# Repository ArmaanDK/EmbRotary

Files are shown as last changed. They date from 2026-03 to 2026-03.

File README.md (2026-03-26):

# EmbRotary
Designing a motorized base that can turn embroidery hoops at variable rates.

## Design Criteria
- Hold three embroidery hoops upright
- Spin embroidery hoops at distinct rotational speeds
- Easy to build
- Use 3D printed hoops that max-out the printbed of a Creality Ender 3 V2

## Plan
A 3D printed base that houses three continuous servo motors, a Raspberry Pi Pico, and three rotary potentiometers for speed control.
The hoops will slide into crevices from the top of the box, interfacing with a bearing-mounted pinion gear and a driving pinion gear attached to a continuous servo.
A USB-C PD power supply (5VDC/3A) powers the device, supplying a 5VDC power rail for the three continuous servos and Raspberry Pi Pico.
Three potentiometers connect, in parallel, between the Pico's 3V3 output and GND, with their wipers connected to three ADC pins on the Pico.

## Mechanical Description
A shaftless, vertical oriented, gravity-preloaded, free-floating spur gear is supported by meshing with two pinion gears below it.
One pinion gear is motor-driven, applying a tangential force to spin the spur gear.
The second pinion gear is a bearing-supported idler pinion which is positioned contralaterally to the driven pinion so the spur gear rotates around its own center axis.
Currently exploring a tapered retaining double-flange design for the pinion gears to provide a lateral restoring force to oppose axial migration of the spur gear.

## Documentation
- [Hardware Selection](Hardware/HardwareSelection.md) - component choices and rationale
- [Bill of Materials](Hardware/BOM.md) - parts list with quantities
- [Wiring / Pin Assignments](Hardware/Wiring.md) - GPIO pin assignments and power connections
- [Software Setup](Software/SETUP.md) - flashing MicroPython and deploying the script

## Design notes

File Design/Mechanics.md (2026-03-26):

# Mechanics

## Gears
### Description
The spur gear is positioned vertically and gravity-preloaded, held down by its own weight without an axle, meshing into two pinion gears below it.
Two pinion gears are positioned contralaterally, opposite to each other across the spur gear's sagittal<sup>[1](#footnote1)</sup> plane, providing opposing tangential and radial reaction forces.
Both pinion gears providing opposing reaction forces prevents radial or tangential translation of the spur gear's center.
Tapered retaining flanges on the pinion gears provides lateral restoring forces to oppose axial translation.
The driven pinion gear applies a tangential force on the teeth of the spur gear as well as a radial force from being positioned laterally from the spur gear's sagittal<sup>[1](#footnote1)</sup> plane.
Simultaneously, the idler pinion's contralateral opposing tangential and radial reaction forces combine with the driven pinion's, forming a force couple.
The combined forces of the two pinions apply a pure moment on the central spur gear, causing pure rotation about its geometric center.

### Specifications
#### Spur Gear
 - Standard: Metric
 - Pressure Angle: 20 deg
 - Module: 6.00
 - Number of Teeth: 30
 - Backlash: 0.00 mm
 - Root Fillet Radius: 2.00 mm
 - Gear Thickness: 10.00 mm
 - Pitch Diameter: 180.0 mm

### Analysis
The gravity-preload must exceed the radial separating force for the gears to retain their mesh without the spur gear lifting off.

$F_{r} = F_{t} \cdot \tan{\phi}$

---
<a name="footnote1">1</a>: More technically referred to as the diametral plane

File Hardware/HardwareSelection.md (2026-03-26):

# Hardware Selection
A breakdown of the hardware selected, as well as the rationale for each selection.

## Motors
Feetech FT90R
- Servos rotate at a slower rate than DC motors
- Can be more easily controlled without needing a complex motor control board handling PWM and transient protection
- Quick and easy to source on Amazon.ca for cross-country parallel building
- Adequate performance without breaking the budget ($29.98CAD for 4)

## Speed Control
Generic 10kΩ Linear Taper Rotary Potentiometers (×3)
- Linear taper gives a proportional voltage output across the full rotation range, making speed feel intuitive to the user
- 10kΩ resistance keeps current draw from the 3V3 rail negligible (~0.33 mA per pot at full deflection)
- Three pots in parallel draw at most ~1 mA total from 3V3 — well within the Pico's 300 mA output limit
- Standard jellybean value, available at any electronics retailer

## Microcontroller
Raspberry Pi Pico
- Jellybean part (~$4USD from raspberrypi.com)
- Adequate GPIO and ADC inputs for project
- MicroPython has more human-readable code for understandability outside of the technological field
- Accepts 5VDC input without needing stepping-down from an external circuit

## Power Cleaning
### Capacitors
Transients from servos when PWM triggers movement can drop the power rail voltage

#### Bulk Input Capacitor
Softens the startup, spec'd for a worst-case scenario of all motors stalling and the Pico at max power consumption (very unrealistic).

Three servos with spec'd stalling currents of $700mA @ 4.8V$ and $800mA @ 6V$, linearly interpolating:

$700 + \frac{800 - 700}{6 - 4.8}(5 - 4.8) = 716.7mA$

$3 \times 716.7mA = 2150mA$

Worst-case scenario spec for Raspberry Pi Pico @ 5V is 95.5 mA,

$I_{T} = I_{Servos} + I_{Pico}$

$I_{T} = 2150mA + 95.5mA = 2245.5mA$

Assuming a $100 \mu s$ response from the power supply and a goal voltage change of less than 5%,

$C = \frac{2.25 A \times 0.0001 s}{5V \times 0.05} = 900 \mu F $

Indicating a minimum $1000 \mu F$ capacitor would be appropriate for the bulk input capacitor.

#### Servo Decoupling Capacitors
Handles transients per-motor going back to the power rail.

$C = \frac{0.7167 \times 0.0001 s}{5V \times 0.05} = 286.7 \mu F$

Since the bulk capacitor will also handle transients, we can rely on $100-220 \mu F$ capacitors instead.

#### Servo Noise Abatement
Expected noise from PWM servo control is in the 10s of MHz range. Adding $100nF$ ceramic capacitors in parallel to the decoupling capacitors will help mitigate high-frequency switching noise from making its way to the power rail.

## Power Supply
[USB-C PD 65W Wall Adapter](https://www.amazon.ca/dp/B0DL5JJS5T), 5VDC/3A output connected directly to the device
- Intended for use as an art installation, so the power source needs to be flexible regardless of venue
- USB-C PD is compatible with a wide range of wall adapters and battery banks, allowing the piece to run from standard wall outlets or a portable battery depending on the display location
- A proprietary barrel jack wall adapter would tie the installation to a specific plug and power source
- USB-C PD negotiates 5V as its baseline profile, reliably delivering the required 5V/3A (15W — well within the 65W capacity of the selected adapter)

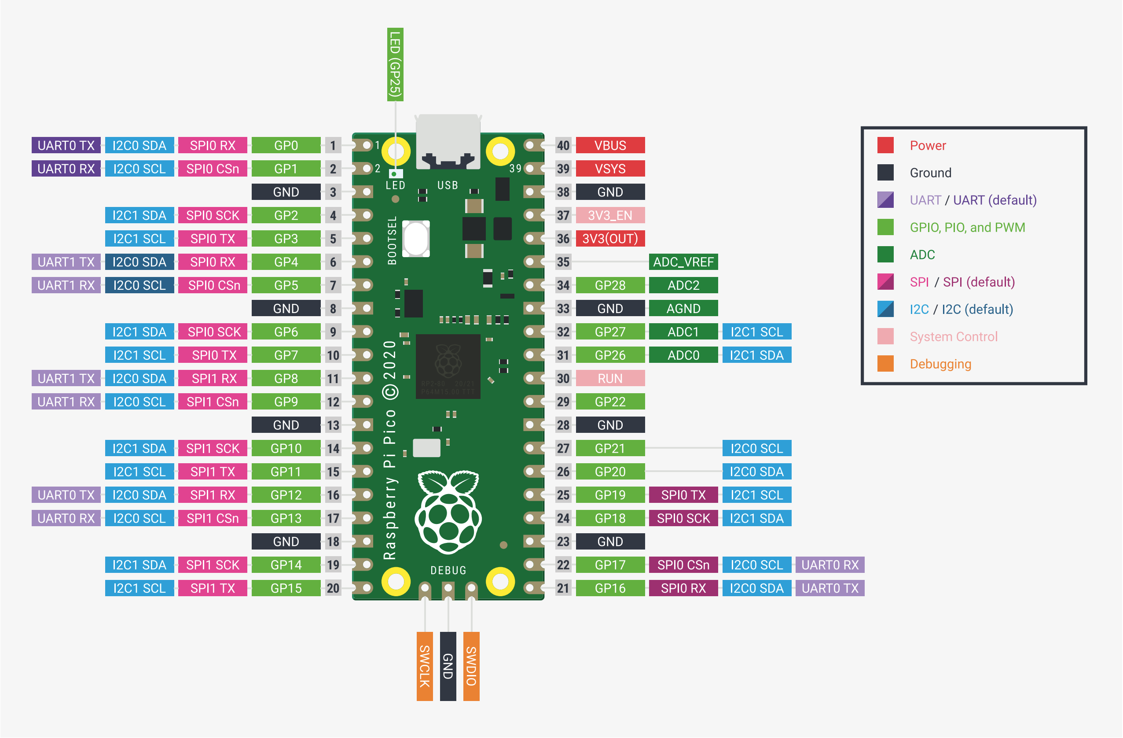
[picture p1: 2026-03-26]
Hardware/PI-PICO_PINOUT.png

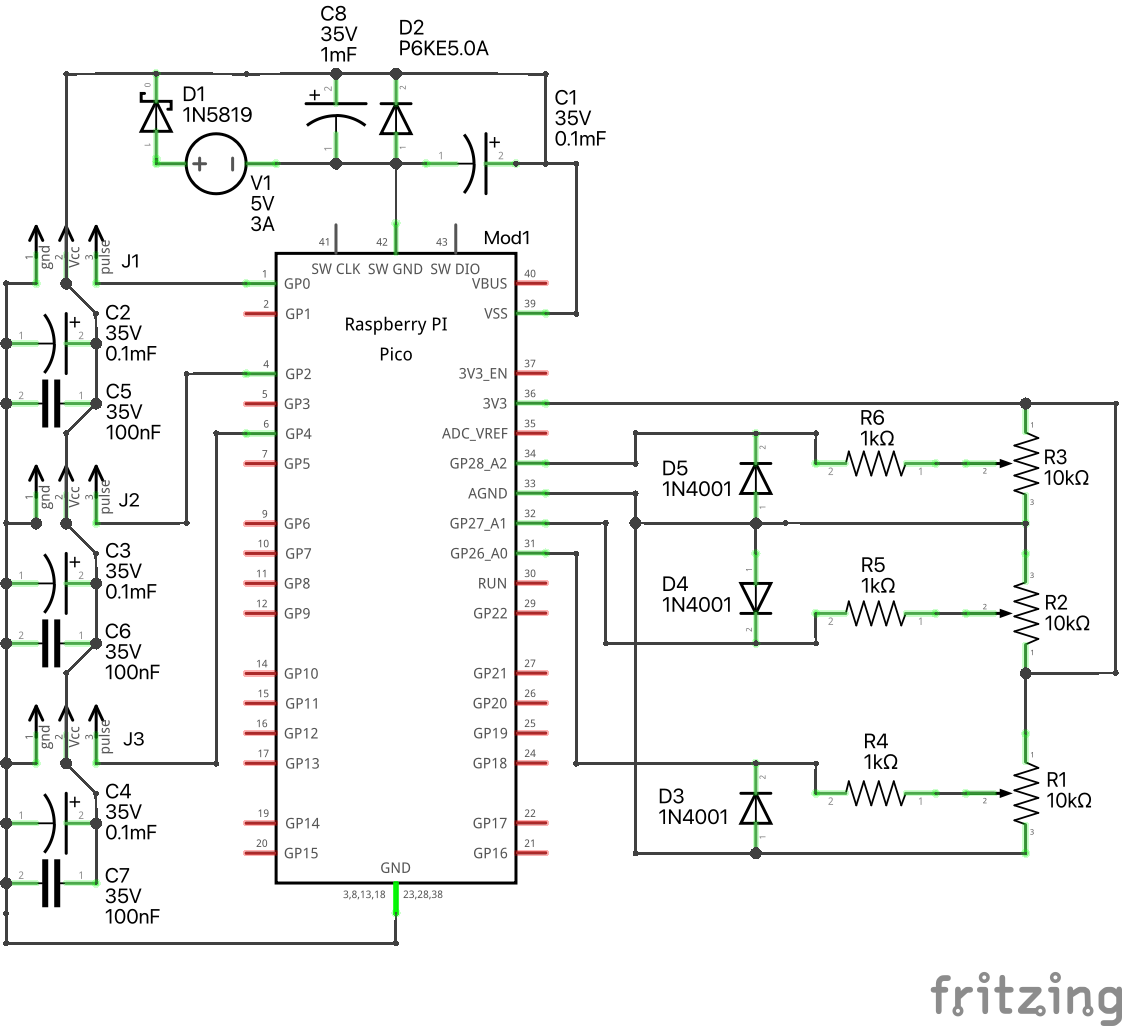
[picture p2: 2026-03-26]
Hardware/EmbRotary_Circuit_schem.png

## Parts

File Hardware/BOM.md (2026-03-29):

# Bill of Materials

Complete parts list for one EmbRotary unit.

---

## Power Path 

| | Path A — USB-C | Path B — DC Barrel Jack |
|---|---|---|
| **Soldering required?** | No | Yes |
| **Best for** | Prototyping / artist build | Permanent enclosure build |

Items marked **[A]** or **[B]** below apply only to that path. Unmarked items are required for both.

---

## Electronics

| Qty | Part | Value / Notes | Source |
|-----|---|---|---|
| 3 | Feetech FT90R Continuous Rotation Servo | Sold in 4-packs; 1 spare | [Amazon.ca][servo] |
| 1 | Raspberry Pi Pico | Pre-soldered headers recommended | [Amazon.ca][pico] |
| 3 | Rotary Potentiometer | 10kΩ linear taper, 15mm shaft (WH148) | [Amazon.ca][pots] |
| 3 | Potentiometer Knob | 6mm knurled shaft, 15×17mm — fits WH148 | [Amazon.ca][knobs] |
| 1 | Electrolytic Capacitor, 1000µF 25V | Bulk input decoupling | [Amazon.ca][ecaps] |
| 3 | Electrolytic Capacitor, 220µF 25V | Per-servo decoupling | [Amazon.ca][ecaps] |
| 3 | Ceramic Capacitor, 100nF | Per-servo high-frequency noise filter | [Amazon.ca][ccaps] |
| 1 | Schottky Diode | D1 — reverse polarity protection; 1N5819 | [Amazon.ca][diodes] |
| 4 | Rectifier Diode | D2–D5; 1N4001 or equivalent | [Amazon.ca][diodes] |
| 1 | Zener Diode | 3.3V BZX55C3V3 — ADC input clamping | [Amazon.ca][zener] |
| 1 | TVS Diode | P6KE6.8A, 600W — transient suppression | [Amazon.ca][tvs] |
| 3 | Resistor, 1kΩ | R4, R5, R6 — current limiting on ADC lines | [Amazon.ca][resistors] |

> Capacitors, diodes, and resistors are sold in assortment kits containing far more than one unit requires. Surplus can be shared between builds.

---

## Power

| Qty | Part | Value / Notes | Source |
|-----|---|---|---|
| 1 | USB-C Power Supply **[A]** | 5V/3A — plug-in, no soldering | [Amazon.ca][usbc-supply] |
| 1 | DC Wall Adapter **[B]** | 5V/3A, 5.5×2.1mm barrel jack output | [Amazon.ca][dc-supply] |
| 1 | Panel-Mount USB-C Socket **[B]** | 6-pin flush mount, PD 65W — soldered to hookup wire, nut-mounted to enclosure | [Amazon.ca][usbc-panel] |
| 1 | Hookup Wire Kit | 22 AWG, 7 colours, 26ft/spool | [Amazon.ca][wire] |
| 1 | Breadboard + Jumper Wire Kit **[A]** | 830+400pt boards, 200+ jumper wires | [Amazon.ca][breadboard] |

---

## Mechanical

| Qty | Part | Notes | Source |
|-----|---|---|---|
| 1 | 3D Printed Parts | Base, pinion gears, hoops — print files in `/Design` | See `/Design` |
| 6 | 625ZZ Ball Bearing | 5×16×5mm — drive and idler pinion per hoop (2× per hoop) | [Amazon.ca][bearings] |
| 1 | M2/M3/M4/M5 Screw Assortment | Alloy steel, black oxide — all printed assembly hardware | [Amazon.ca][screws] |
| 1 | Wood PLA Filament Bundle | 1.75mm, 30%+ real wood fibre, 4×200g — current print material | [Amazon.ca][filament] |

---

[servo]: https://www.amazon.ca/dp/B07JDR2HH5
[pico]: https://www.amazon.ca/Freenove-Raspberry-Compatible-Pre-Soldered-Development/dp/B09X33TBY3/
[pots]: https://www.amazon.ca/dp/B09XDR799P
[knobs]: https://www.amazon.ca/dp/B0C14MGL4B
[ecaps]: https://www.amazon.ca/dp/B0C1VBXCQM
[ccaps]: https://www.amazon.ca/dp/B08DNF191P
[diodes]: https://www.amazon.ca/dp/B08F2LHDZ7
[zener]: https://www.amazon.ca/dp/B07WDR4DBN
[tvs]: https://www.amazon.ca/dp/B0FRMZ2G2X
[resistors]: https://www.amazon.ca/ELEGOO-Resistor-Assortment-Compliant-Respberry/dp/B072BL2VX1/
[screws]: https://www.amazon.ca/dp/B0D6347484
[bearings]: https://www.amazon.ca/dp/B0CJFSBRTJ
[usbc-supply]: https://www.amazon.ca/Miuzei-Raspberry-Pi-Power-Supply/dp/B09WYRFWMW/
[dc-supply]: https://www.amazon.ca/BTF-LIGHTING-Certified-Transformer-Converter-SK6812RGBW/dp/B0G8JQ1FJ7/
[usbc-panel]: https://www.amazon.ca/dp/B0DL5JJS5T
[breadboard]: https://www.amazon.ca/Breadboards-Include-Solderless-Jumper-Tweezer/dp/B0BMFXPSVG/
[wire]: https://www.amazon.ca/dp/B083DN5R61
[filament]: https://www.amazon.ca/dp/B0C85SS6FT

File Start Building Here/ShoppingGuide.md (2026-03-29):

# EmbRotary - Quick Shopping Guide

---

## Step 1 — One Question First

**Do you have access to a soldering iron?**

- **No -> you're on Path A.** Skip the items marked [B] below.
- **Yes -> you're on Path B.** Skip the items marked [A] below.

---

## Step 2 — Order Everything on This List

### Core Electronics

| What | Price | Link |
|---|---|---|
| Feetech FT90R Servo (4-pack, 3 used) | CA$29.98 | [Amazon.ca][servo] |
| Raspberry Pi Pico (pre-soldered headers) | CA$17.95 | [Amazon.ca][pico] |
| 10kΩ Potentiometer WH148 (30-pack, 3 used) | CA$13.61 | [Amazon.ca][pots] |
| Potentiometer Knob 6mm (60-pack, 3 used) | CA$7.69 | [Amazon.ca][knobs] |

### Circuit Components *(kits — one purchase covers everything)*

| What | Price | Link |
|---|---|---|
| Electrolytic Capacitor Kit | CA$18.99 | [Amazon.ca][ecaps] |
| Ceramic Capacitor Kit | CA$24.99 | [Amazon.ca][ccaps] |
| Rectifier + Schottky Diode Kit | CA$11.25 | [Amazon.ca][diodes] |
| Zener Diode 3.3V (20-pack) | CA$8.00 | [Amazon.ca][zener] |
| TVS Diode P6KE6.8A (20-pack) | CA$9.00 | [Amazon.ca][tvs] |
| Resistor Kit (525-pack) | CA$13.99 | [Amazon.ca][resistors] |

### Mechanical

| What | Price | Link |
|---|---|---|
| 625ZZ Bearings 5×16×5mm (15-pack, 6 used) | CA$11.19 | [Amazon.ca][bearings] |
| M2–M5 Screw Assortment (860-piece) | CA$14.99 | [Amazon.ca][screws] |
| Wood PLA Filament Bundle 1.75mm, 4×200g | CA$39.99 | [Amazon.ca][filament] |

### Power + Wiring

| What | Price | Link |
|---|---|---|
| Miuzei USB-C Power Supply 5V/3A **[A]** | CA$17.99 | [Amazon.ca][usbc-supply] |
| Breadboard + Jumper Wire Kit **[A]** | CA$19.99 | [Amazon.ca][breadboard] |
| DC Wall Adapter 5V/3A barrel jack **[B]** | CA$17.09 | [Amazon.ca][dc-supply] |
| Panel-Mount USB-C Socket (5-pack) **[B]** | CA$19.11 | [Amazon.ca][usbc-panel] |
| 22 AWG Hookup Wire Kit | CA$21.98 | [Amazon.ca][wire] |

---

## Step 3 — Print the Parts

Print files are in the `/Design` folder of the repository. Use the Wood PLA filament ordered above.

---

[servo]: https://www.amazon.ca/dp/B07JDR2HH5
[pico]: https://www.amazon.ca/Freenove-Raspberry-Compatible-Pre-Soldered-Development/dp/B09X33TBY3/
[pots]: https://www.amazon.ca/dp/B09XDR799P
[knobs]: https://www.amazon.ca/dp/B0C14MGL4B
[ecaps]: https://www.amazon.ca/dp/B0C1VBXCQM
[ccaps]: https://www.amazon.ca/dp/B08DNF191P
[diodes]: https://www.amazon.ca/dp/B08F2LHDZ7
[zener]: https://www.amazon.ca/dp/B07WDR4DBN
[tvs]: https://www.amazon.ca/dp/B0FRMZ2G2X
[resistors]: https://www.amazon.ca/ELEGOO-Resistor-Assortment-Compliant-Respberry/dp/B072BL2VX1/
[bearings]: https://www.amazon.ca/dp/B0CJFSBRTJ
[screws]: https://www.amazon.ca/dp/B0D6347484
[filament]: https://www.amazon.ca/dp/B0C85SS6FT
[usbc-supply]: https://www.amazon.ca/Miuzei-Raspberry-Pi-Power-Supply/dp/B09WYRFWMW/
[breadboard]: https://www.amazon.ca/Breadboards-Include-Solderless-Jumper-Tweezer/dp/B0BMFXPSVG/
[dc-supply]: https://www.amazon.ca/BTF-LIGHTING-Certified-Transformer-Converter-SK6812RGBW/dp/B0G8JQ1FJ7/
[usbc-panel]: https://www.amazon.ca/dp/B0DL5JJS5T
[wire]: https://www.amazon.ca/dp/B083DN5R61

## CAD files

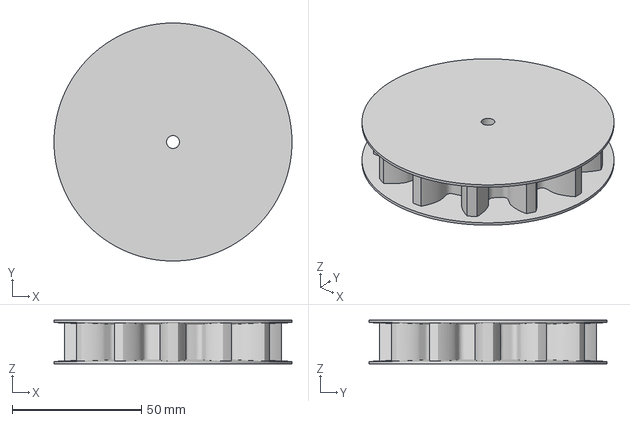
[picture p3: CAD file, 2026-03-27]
Design/Reference Models/Pinion (12 teeth).3mf
92.0 x 92.0 x 17.0 mm

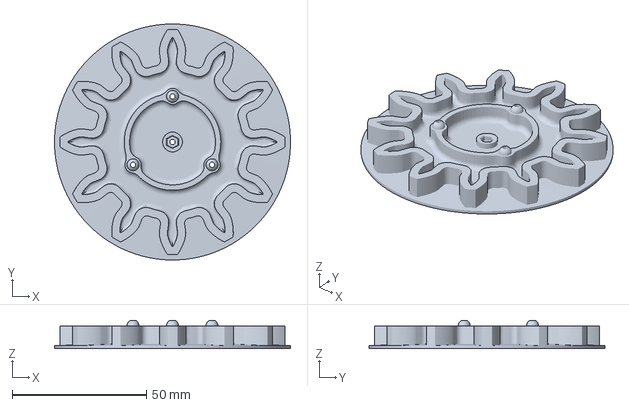
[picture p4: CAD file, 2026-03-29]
Start Building Here/PrintFiles/Half Pinion Gears/Pinion-Idler-S2.3mf
88.0 x 88.0 x 10.5 mm

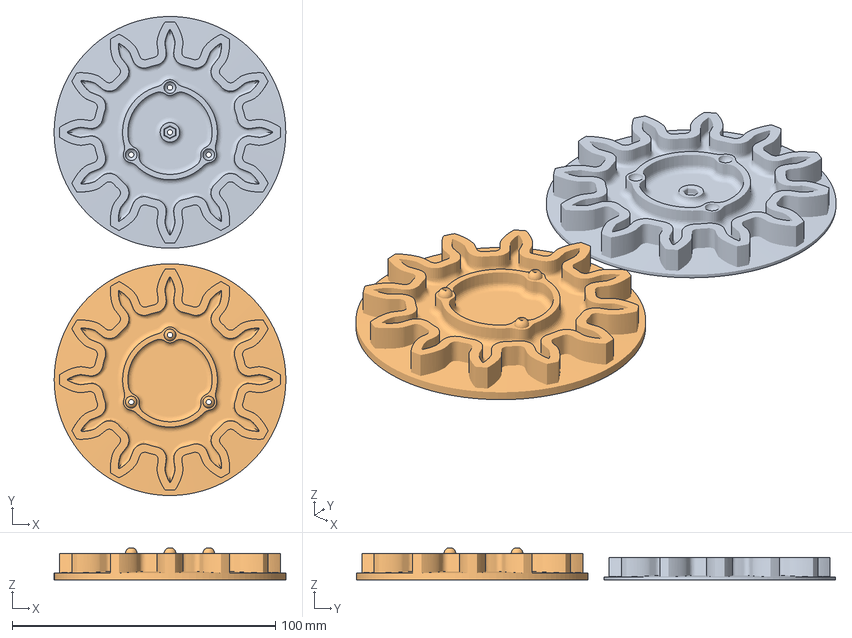
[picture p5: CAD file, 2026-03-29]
Start Building Here/PrintFiles/Pinion-Driver.3mf
88.0 x 182.0 x 12.0 mm
Pinion-Idler-S1
Pinion-Driver

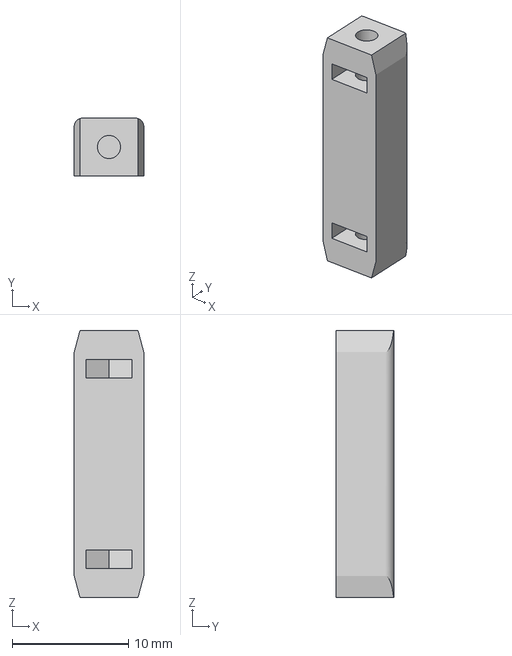
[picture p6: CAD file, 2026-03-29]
Start Building Here/PrintFiles/23mm-Connector.3mf
6.00 x 5.00 x 23.0 mm

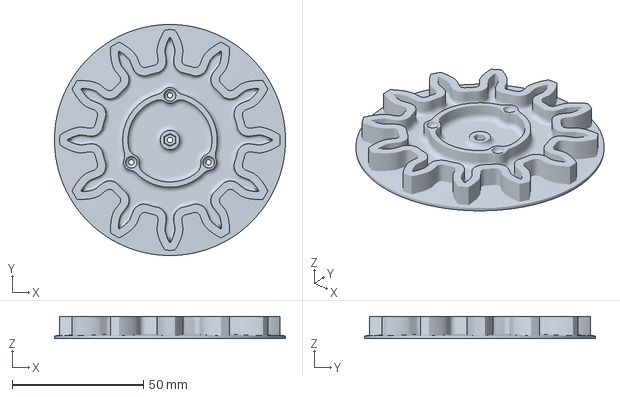
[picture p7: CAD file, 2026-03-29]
Start Building Here/PrintFiles/Half Pinion Gears/Pinion-Idler-S1.3mf
88.0 x 88.0 x 8.50 mm

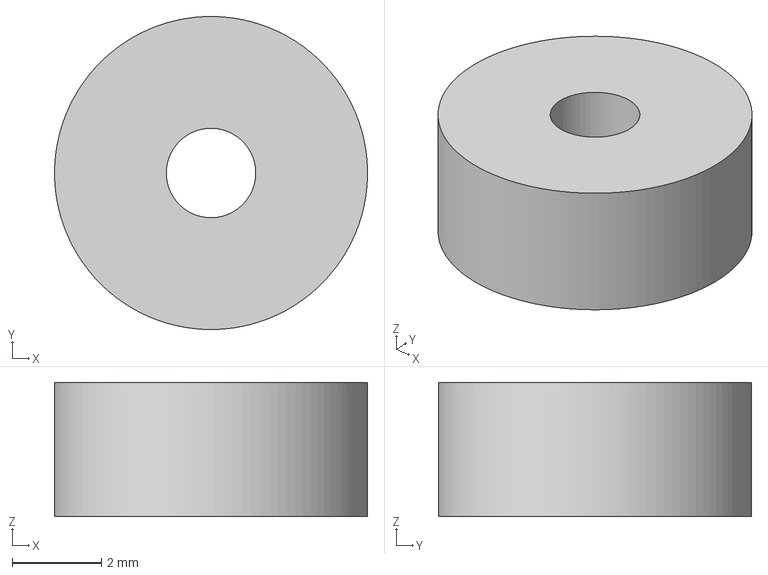
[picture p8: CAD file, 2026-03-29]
Start Building Here/PrintFiles/AxleSpacer.3mf
7.00 x 7.00 x 3.00 mm

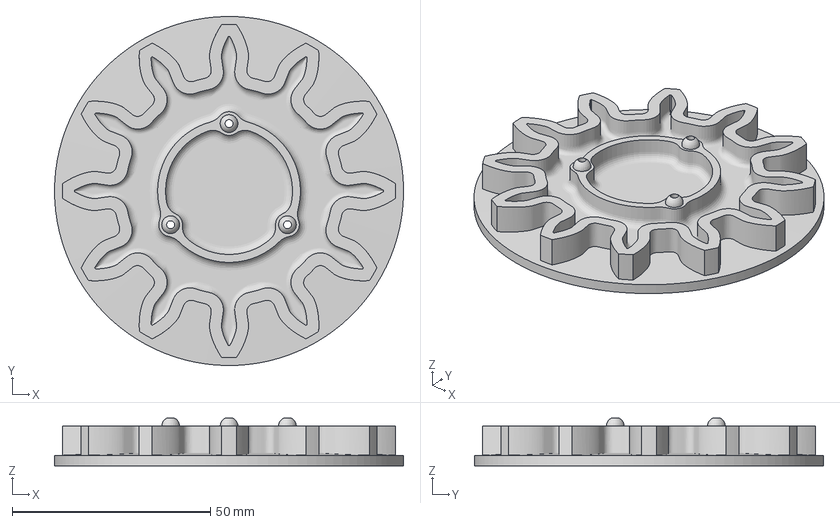
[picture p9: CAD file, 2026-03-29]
Start Building Here/PrintFiles/Half Pinion Gears/Pinion-Driver.3mf
88.0 x 88.0 x 12.0 mm

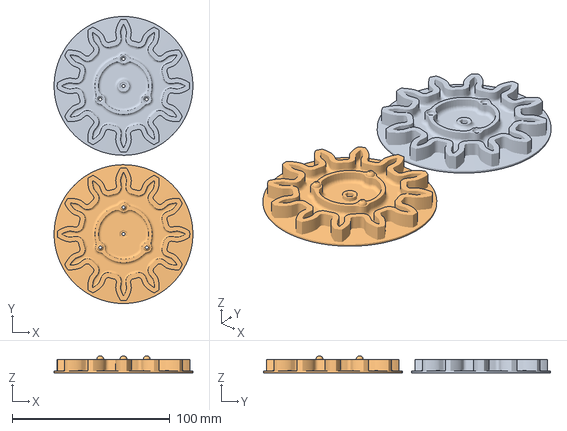
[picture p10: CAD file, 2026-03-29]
Start Building Here/PrintFiles/Pinion-Idler.3mf
88.0 x 182.0 x 10.5 mm
Pinion-Idler-S1
Pinion-Idler-S2

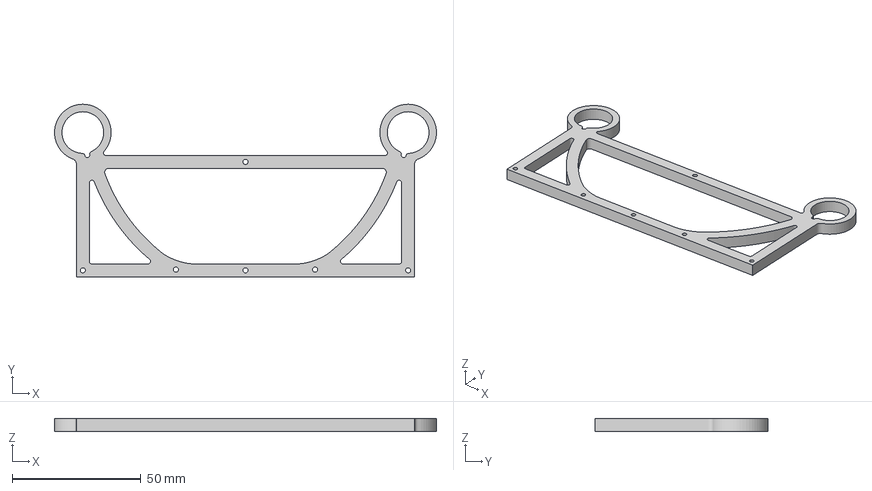
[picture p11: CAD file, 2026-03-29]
Start Building Here/PrintFiles/BaseBearings.3mf
148.3 x 67.0 x 5.00 mm

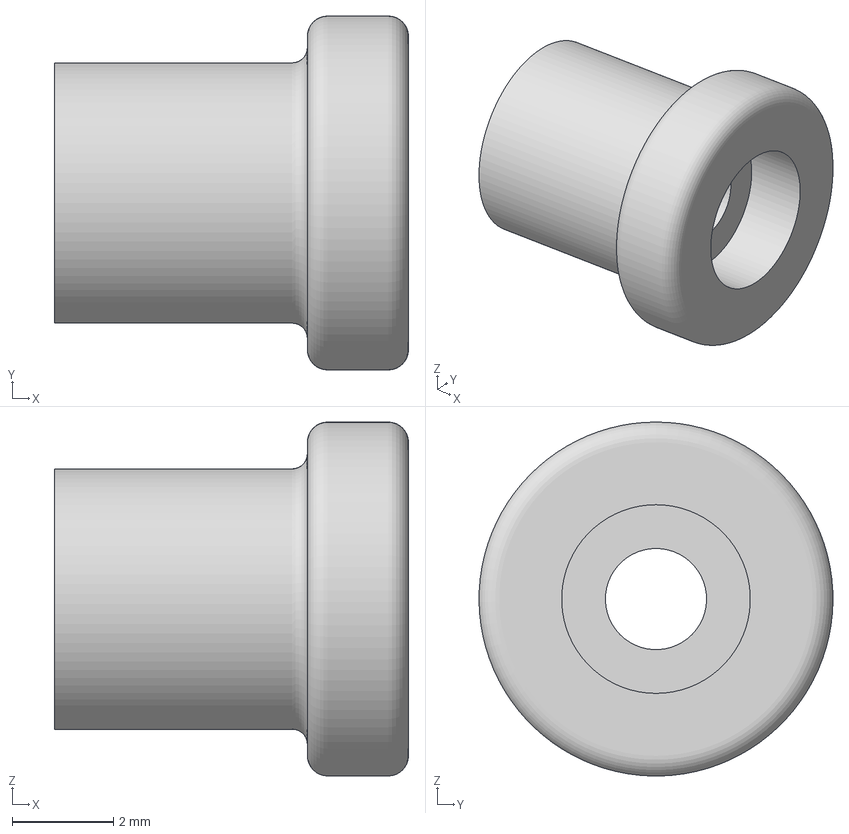
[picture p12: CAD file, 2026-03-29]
Start Building Here/PrintFiles/BearingPlug.3mf
7.00 x 7.00 x 7.00 mm

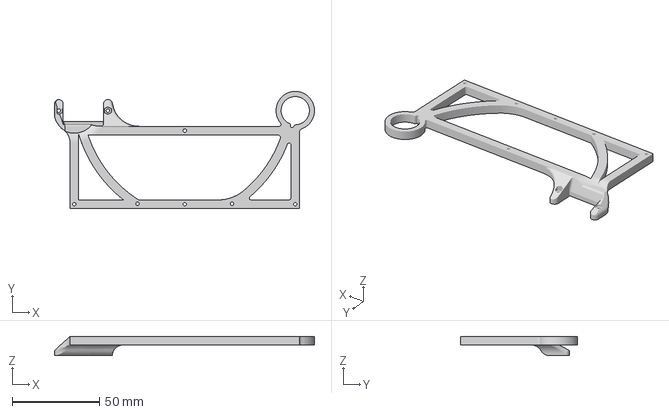
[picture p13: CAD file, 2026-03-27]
Start Building Here/PrintFiles/BaseServo.3mf
148.6 x 67.0 x 11.1 mm

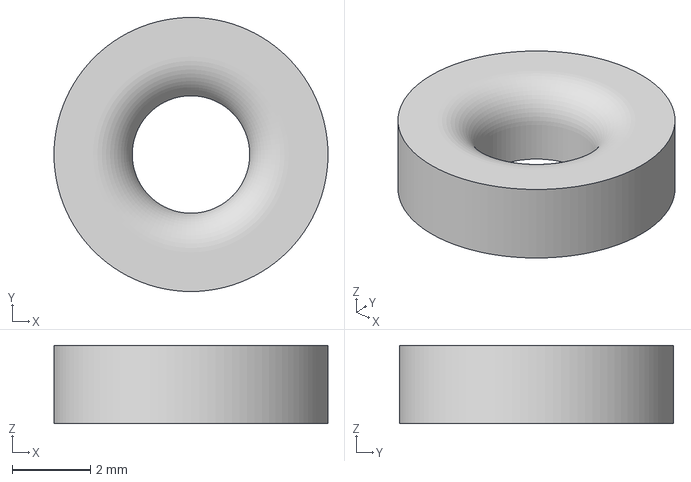
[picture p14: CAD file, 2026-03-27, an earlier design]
Design/Deprecated/AxleSpacer.3mf
7.00 x 7.00 x 2.00 mm

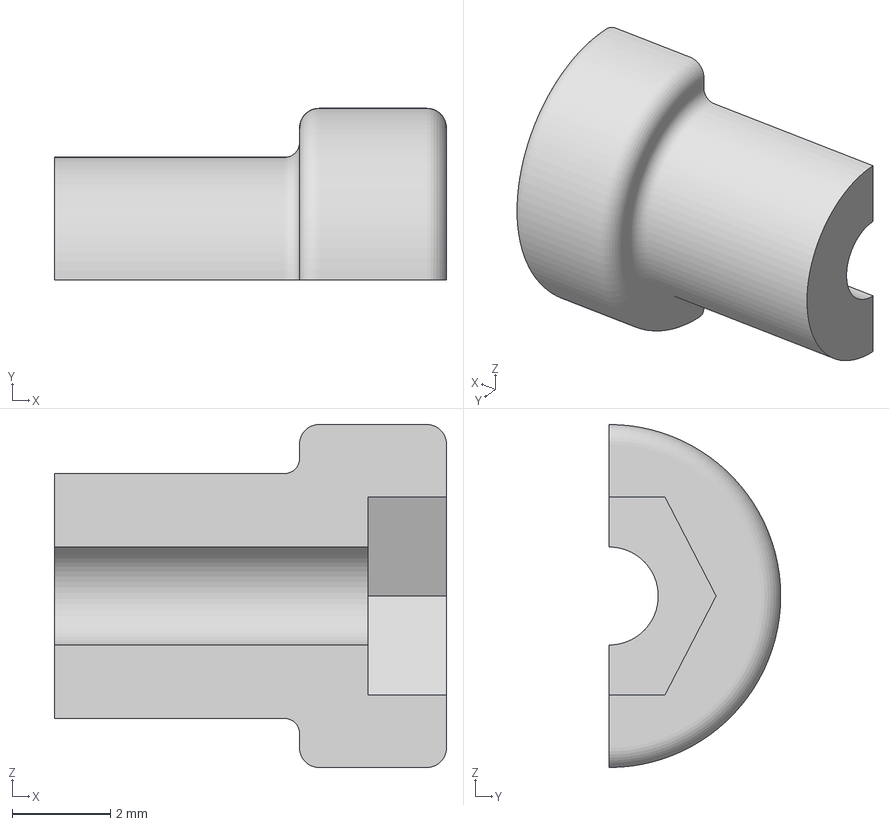
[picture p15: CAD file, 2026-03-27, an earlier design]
Design/Deprecated/BearingPlugSectioned.3mf
8.00 x 3.50 x 7.00 mm

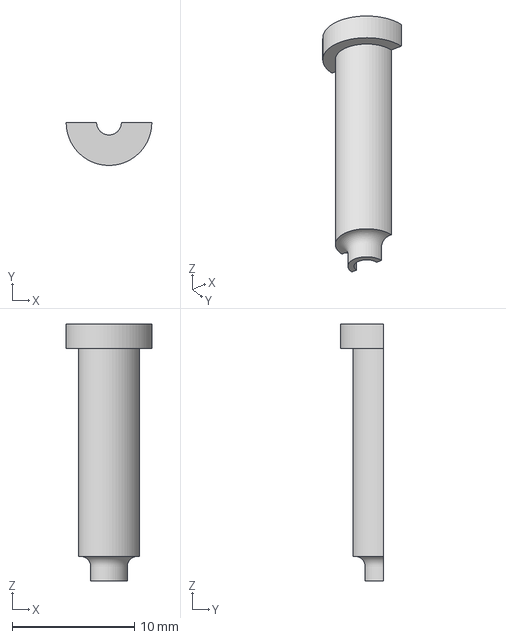
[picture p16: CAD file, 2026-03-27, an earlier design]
Design/Deprecated/HalfAxle.3mf
7.00 x 3.50 x 21.0 mm

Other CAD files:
Design/Deprecated/BearingPlug.3mf
Design/Deprecated/TestBaseFrictionFit.3mf
Design/Deprecated/20mm Connector.3mf
Design/Deprecated/TestBaseFrictionFit_Notched.3mf
Design/Deprecated/20mm Connector Wider.f3z
Design/Deprecated/21mm Connector.f3z
Design/Deprecated/AxleSpacer.f3d
Design/Deprecated/BearingPlug.f3d
Design/Deprecated/Draft Layout Assembly.f3z
Design/Deprecated/HalfAxle.f3d
Design/Deprecated/Pinion (12 teeth).f3d
Design/Deprecated/gear project.f3d
Design/Fusion Files/23mm Connector.f3z
Design/Fusion Files/AxleSpacer.f3d
Design/Fusion Files/BaseBearings.f3d
Design/Fusion Files/BearingPlug.f3d
Design/Fusion Files/Pinion-Driver.f3z
Design/Fusion Files/Pinion-Idler-S1.f3z
Design/Fusion Files/Pinion-Idler-S2.f3z
Design/Reference Models/Disc Servo Attachment.f3d
Design/Reference Models/FT90R (Assembly).f3z
Design/Reference Models/Pinion (12 teeth).f3z
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

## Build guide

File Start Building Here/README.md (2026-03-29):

# Building Instructions

EmbRotary

As at March 29th, 2026

Note that the assembly for the fully-assembled base can be found in [`../Design/Base Assembly.f3z`](/Design/Base%20Assembly.f3z) and should be referred to when instructions are unclear.
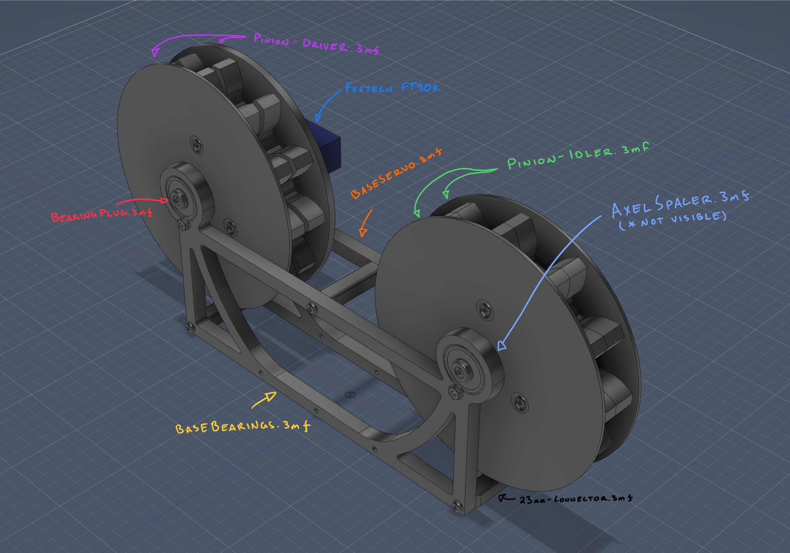
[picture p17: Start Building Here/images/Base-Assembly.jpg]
Base Assembly


## Parts
### Printed
Mesh files located in `/Print Files`
 - [`23mm-Connector.3mf`](/Start%20Building%20Here/PrintFiles/23mm-Connector.3mf) - Connector which goes between the two base frames (BaseServo and BaseBearings), 3 per base
 - [`AxleSpacer.3mf`](/Start%20Building%20Here/PrintFiles/AxleSpacer.3mf) - Placed between the bearing and pinion gear, 3 per base
 - [`BaseBearings.3mf`](/Start%20Building%20Here/PrintFiles/BaseBearings.3mf) - One of two base frames which holds only the ball bearings, 1 per base
 - [`BaseServo.3mf`](/Start%20Building%20Here/PrintFiles/BaseServo.3mf) - One of the two base frames which holds one ball bearing and one Feetech FT90R, 1 per base
 - [`BearingPlug.3mf`](/Start%20Building%20Here/PrintFiles/BearingPlug.3mf) - Acts as sleeve for M2 screw in ball bearing turning it into an axle, 3 per base
 - [`Pinion-Driver.3mf`](/Start%20Building%20Here/PrintFiles/Pinion-Driver.3mf) - The driver pinion gear which is driven by the servo horn, both halves included in this file, 1 per base
 - [`Pinion-Idler.3mf`](/Start%20Building%20Here/PrintFiles/Pinion-Idler.3mf) - The idler pinion gear which has one bearing on either side, both halves included in this file, 1 per base

 ### Hardware
 - `M2 Nut` - 16 per base
   - 1 per bearing
   - 2 per connector
   - 5 per idler pinion gear
   - 4 per driver pinion gear
 - `M2 Washer` - 6 per base
   - 2 per bearing (1 under screw head, 1 under nut)
 - `M2x8 Screw` - 3 per base
   - 1 per bearing
 - `M2x12 Screw` - 8 per base
   - 2 per connector
   - 2 per servo
 - `M2x16 Screw` - 9 per base
   - 1 per bearing
   - 3 per pinion gear
 - `625ZZ Bearing` - 3 per base
   - 2 per `BaseBearings.3mf`
   - 1 per `BaseServo.3mf`
 - `Feetech FT90R` - 1 per base
   - 1 per `BaseServo.3mf`

## Printing Parts

> All parts can be printed using PETG with:
> 15% infill,
> at least two perimeter shells,
> 4 top and bottom solid layers,
> 0.2 mm layer height for speed,
> brims for thin or small objects

1. Start by printing the base frames, both should be printed flat. The bearing-only base frame (`BaseBearings.3mf`) should not require any supports, unlike the servo base frame (`BaseServo.3mf`) which should be oriented such that the servo mounting point is floating above the printer bed to minimize the support material used.
2. Print the connectors (`23mm Connector.3mf`), three (or more) can be printed at a time. The connectors should be printed with the entry point for the M2 nuts facing up to remove the need for support materials.
3. You can now print the driver pinion gear (`Pinion-Driver.3mf`) and the idler pinion gear (`Pinion-Idler.3mf`), one after the other. Each `.3mf` file contains both halves on a single bed to reduce the need for printbed resets. With each half laying flange-side down on the printbed, supports should be enabled to reduce the risk of warped servo horn or M2 hardware interfacing surfaces.
4. Now the smaller parts comprising the pinion gear axles can be printed. Each bearing requires one `BearingPlug.3mf` and one `AxleSpacer.3mf`. The bearing plug holds and `M2x16 Screw` and goes into the bearing from the outside, exiting the bearing towards the pinion gear. Between the bearing and pinion gear, place a spacer to help align the two pinions and avoid interacting with other hardware such as the bearing mount screws. Testing shows each plug and spacer prints well alone, the ability to print multiple on a single bed depends on the individual printer's ability to handle multiple thin objects. The bearing plug should be placed on the bed with the fat side facing down and using both supports and a brim. The axle spacer should be placed flat and should also require a brim.

## Assembly
1. After printing the base frames, it's best to start by inserting the bearings. First, insert the bearings such that they are flush with the base frames. Next, take an `M2x8 Screw` and place an `M2 Washer` below the head before screwing it into the notch below the bearing from the pinion gear side of the frame. We screw in from the pinion gear side to minimize the protruding length since the exiting end which will go through the nut is longer than the head and washer. Once the threads begin to pop out from the other side of the frame, place another `M2 Washer` on the screw before screwing on an `M2 Nut`. Repeat two more times, each `BaseServo.3mf` requires one bearing and each `BaseBearings.3mf` requires two.
2. Next, we can attach the `Feetech FT90R` to our `BaseServo.3mf`. Be sure to remove any support material from the part, especially in the two pinion-facing surfaces of the servo mount itself, as those holes are cut to the shape of an `M2 Nut` to both make attachment easier and also better hold the fastened screw in place. First, it is much easier to attach the servo when the horn is uninstalled- so make sure the servo is free from any attachments. Next, it is easiest to screw the servo into the frame without trying to hold the nut in place. Insert the servo from the non-pinion side of the base frame. Insert two `M2x12 Screw` through the servo's mounting holes into the frame's holes and at least partially screw them in before trying to fasten them with the nuts. Then- hold the nut, one at a time, with your left index finger, while using the allen key to screw each `M2x12 Screw` through their respective `M2 Nut`. Once positively affixed, attach the servo horn by pressing it onto the servo's shaft as far as it will go before inserting and screwing in the small screw included with the servo along with its horns.
3. After the frames have been populated, we can prepare the connectors which will combine the two base frames into one base per assembly. For each `23mm-Connector.3mf`, insert two `M2 Nut` into the bottom slots. Be careful with the orientation, as the internal cavity is designed so the longest dimension is vertical. That means the nut should not have one of it's flat faces parallel with the surface once it is fully seated.
4. Now we can connect the two base frames using the connectors. Hold each connector in place with your left hand, then insert an `M2x12 Screw` through the frame and screw it in until it goes through the frame and into the connector. It's easiest to do this one frame at a time.
5. After the bases have been screwed together and the pinion gears have been printed, we can prepare the pinion gears for assembly. First things first, thorougly clear out any support material to make sure all fasteners and the servo properly interface with the gears. Next, each half gear that attaches to a bearing has an internal `M2 Nut` that needs to be inserted. After that, the servo-mounting side of the driver pinion gear and one of the two halves of the idler gear has three places to insert `M2 Nut` on their outer surface. Once all nuts are in place, connect each gear half to their partner components. There are locator bumps through which the connection screws travel. Make sure the teeth are aligned between both halves in addition to the locator bumps being seated. Once the two halves are together, insert 3 `M2x16 Screw` on the gear half opposite the ones you just placed the `M2 Nut`s. Tighten the screws until the teeth appear flush and without any gap, ensuring the screw is tightening through the nut. If you don't see the screw exiting it's respective nut, press the nut farther down with a tool like tweezers or a screwdriver.
6. Once all gears are assembled it's time to finalize the assembly! First, place 3 `M2x16 Screw` through the `BearingPlug.3mf`s, making sure they go all the way through to make mounting the pinion gears easier. Next, place the driver gear into its position, nestling the servo horn into its respective notch. Then, place as `AxleSpacer.3mf` between the driver pinion gear and the bearing before inserting the `BearingPlug.3mf` with its `M2x16 Screw` so that the screw end passes through the bearing and spacer before reaching the 2 mm hole of the driver pinion gear. Tighten the screw before moving on to the idler gear. Mount the idler gear the same way you did with the bearing side of the driver pinion gear, first inserting the gear then positioning a spacer between the gear and bearing, finally inserting the bearing plug through the bearing and tightening the screw.

If all goes according to plan, congratulations! You've assembled a base that should spin the spur gear place between the two pinion gears!

Next up is the circuitry which we'll cover later! Note that each base is its own independent unit, extra mounting holes are provided at the bottoms of each base frame to rigidly affix the bases at desired distances.

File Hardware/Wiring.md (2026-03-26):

# Wiring / Pin Assignments

Pin assignments for the Raspberry Pi Pico. See [PI-PICO_PINOUT.png](PI-PICO_PINOUT.png) for the physical pin diagram.

## Potentiometers (Speed Control)

All three potentiometers share the same 3V3 and GND rails (connected in parallel).

| Potentiometer | Wiper → Pico Pin  | Notes |
|---|---|---|
| Pot 1 (Servo 1) | GP26 — ADC0 | |
| Pot 2 (Servo 2) | GP27 — ADC1 | |
| Pot 3 (Servo 3) | GP28 — ADC2 | |
| All pots VCC | 3V3 (pin 36) | Shared rail |
| All pots GND | GND | Shared rail |

## Servos (Feetech FT90R Continuous Rotation)

| Servo | Signal → Pico Pin | Power | Ground |
|---|---|---|---|
| Servo 1 | GP0 — PWM0A | 5V rail | GND |
| Servo 2 | GP2 — PWM1A | 5V rail | GND |
| Servo 3 | GP4 — PWM2A | 5V rail | GND |

## Power

| Connection | Detail |
|---|---|
| Input | USB-C PD (5V/3A) directly into device |
| Pico supply  | VSYS (pin 39) from 5V rail; Pico regulates to 3V3 internally |
| Servo supply | 5V rail directly |
| Pot supply | 3V3 from Pico (pin 36) |

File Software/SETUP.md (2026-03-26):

# Software Setup

How to flash MicroPython onto the Raspberry Pi Pico and deploy the EmbRotary script.

## 1. Flash MicroPython Firmware

1. Download the latest MicroPython UF2 firmware for the Pico from [micropython.org/download/RPI_PICO](https://micropython.org/download/RPI_PICO/)
2. Hold the **BOOTSEL** button on the Pico, then connect it to your computer via USB
3. Release BOOTSEL — the Pico will appear as a mass storage device called **RPI-RP2**
4. Drag and drop the downloaded `.uf2` file onto the RPI-RP2 drive
5. The Pico will reboot automatically into MicroPython (the drive will disappear)

## 2. Deploy main.py

Choose either Thonny (beginner-friendly GUI) or `mpremote` (command line).

### Option A — Thonny

1. Install [Thonny](https://thonny.org/)
2. In Thonny, go to **Tools → Options → Interpreter** and select **MicroPython (Raspberry Pi Pico)**
3. Open `Software/main.py`
4. Click **File → Save As**, choose **Raspberry Pi Pico** as the location, and save as `main.py`
5. The script will run automatically on every power-up

### Option B — mpremote (command line)

```bash
pip install mpremote
mpremote connect auto cp Software/main.py :main.py
```

## 3. Verify

Power cycle the Pico (unplug and replug USB, or disconnect and reconnect the 5V rail).
The servos should respond to the potentiometers immediately on startup — no further interaction needed.

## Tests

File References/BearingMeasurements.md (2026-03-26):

## 625ZZ
OD: 0.630 in -> 16.002 mm
ID: 0.199 in ->  5.055 mm
Th: 0.199 in ->  5.055 mm

## MR115-2RS
OD: 0.433 in -> 10.998 mm
ID: 0.196 in ->  4.978 mm
Th: 0.157 in ->  3.988 mm

## HK0306
OD: 0.257 in ->  6.020 mm
ID: 0.131 in ->  3.327 mm
(Not really, roller bearings aren't contralateral making reading larger than it should be)
Th: 0.231 in ->  5.867 mm

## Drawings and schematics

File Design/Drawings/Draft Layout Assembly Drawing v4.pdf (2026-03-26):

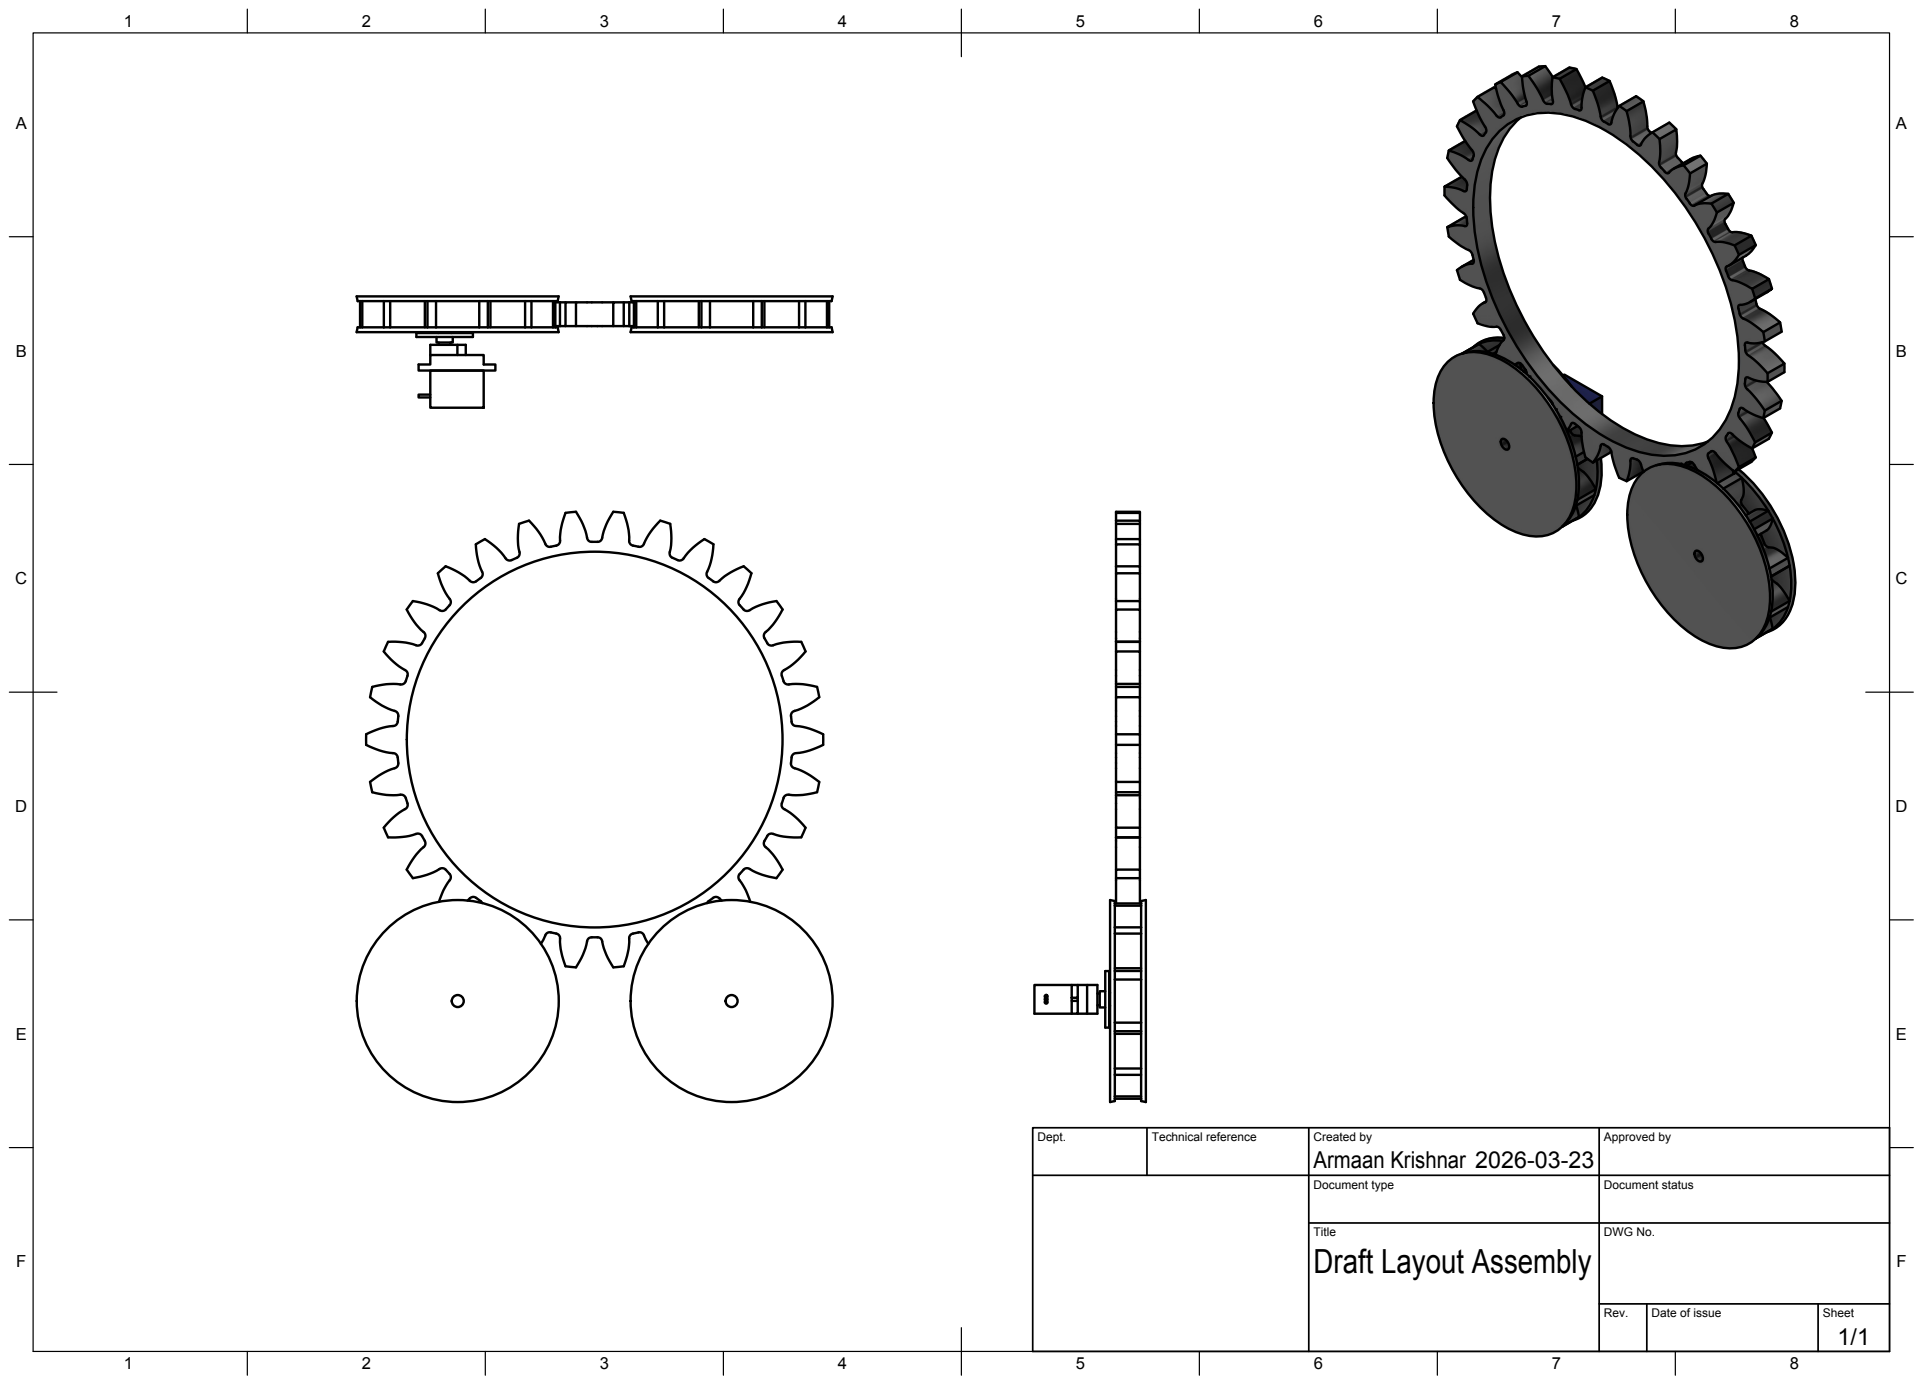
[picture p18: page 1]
Title; DWG No.; Rev.; Date of issue; Sheet

Dept. | Technical reference | Created by Armaan Krishnar 2026-03-23 | Approved by

Document type | Document status

Draft Layout Assembly

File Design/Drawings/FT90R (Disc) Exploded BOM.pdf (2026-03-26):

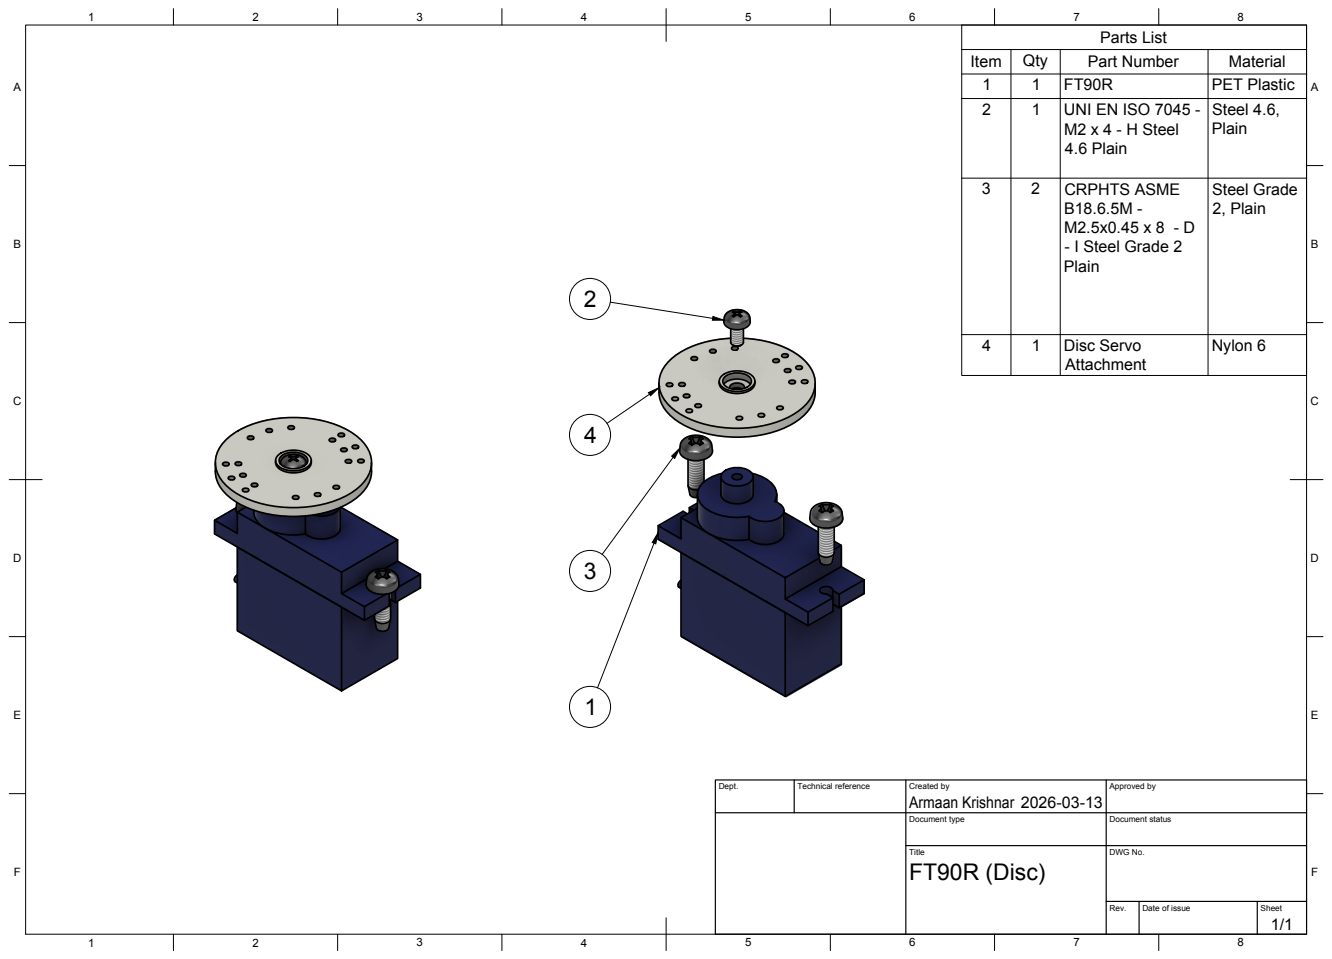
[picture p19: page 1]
Title; DWG No.; Rev.; Date of issue; Sheet; FT90R (Disc); Parts List

Item | Qty | Part Number | Material
1 | 1 | FT90R | PET Plastic
2 | 1 | UNI EN ISO 7045 -M2 x 4 - H Steel 4.6 Plain | Steel 4.6, Plain

3 | 2 | CRPHTS ASME B18.6.5M -M2.5x0.45 x 8 - D - I Steel Grade 2 Plain | Steel Grade 2, Plain

4 | 1 | Disc Servo Attachment | Nylon 6

Dept. | Technical reference | Created by Armaan Krishnar 2026-03-13 | Approved by

Document type | Document status

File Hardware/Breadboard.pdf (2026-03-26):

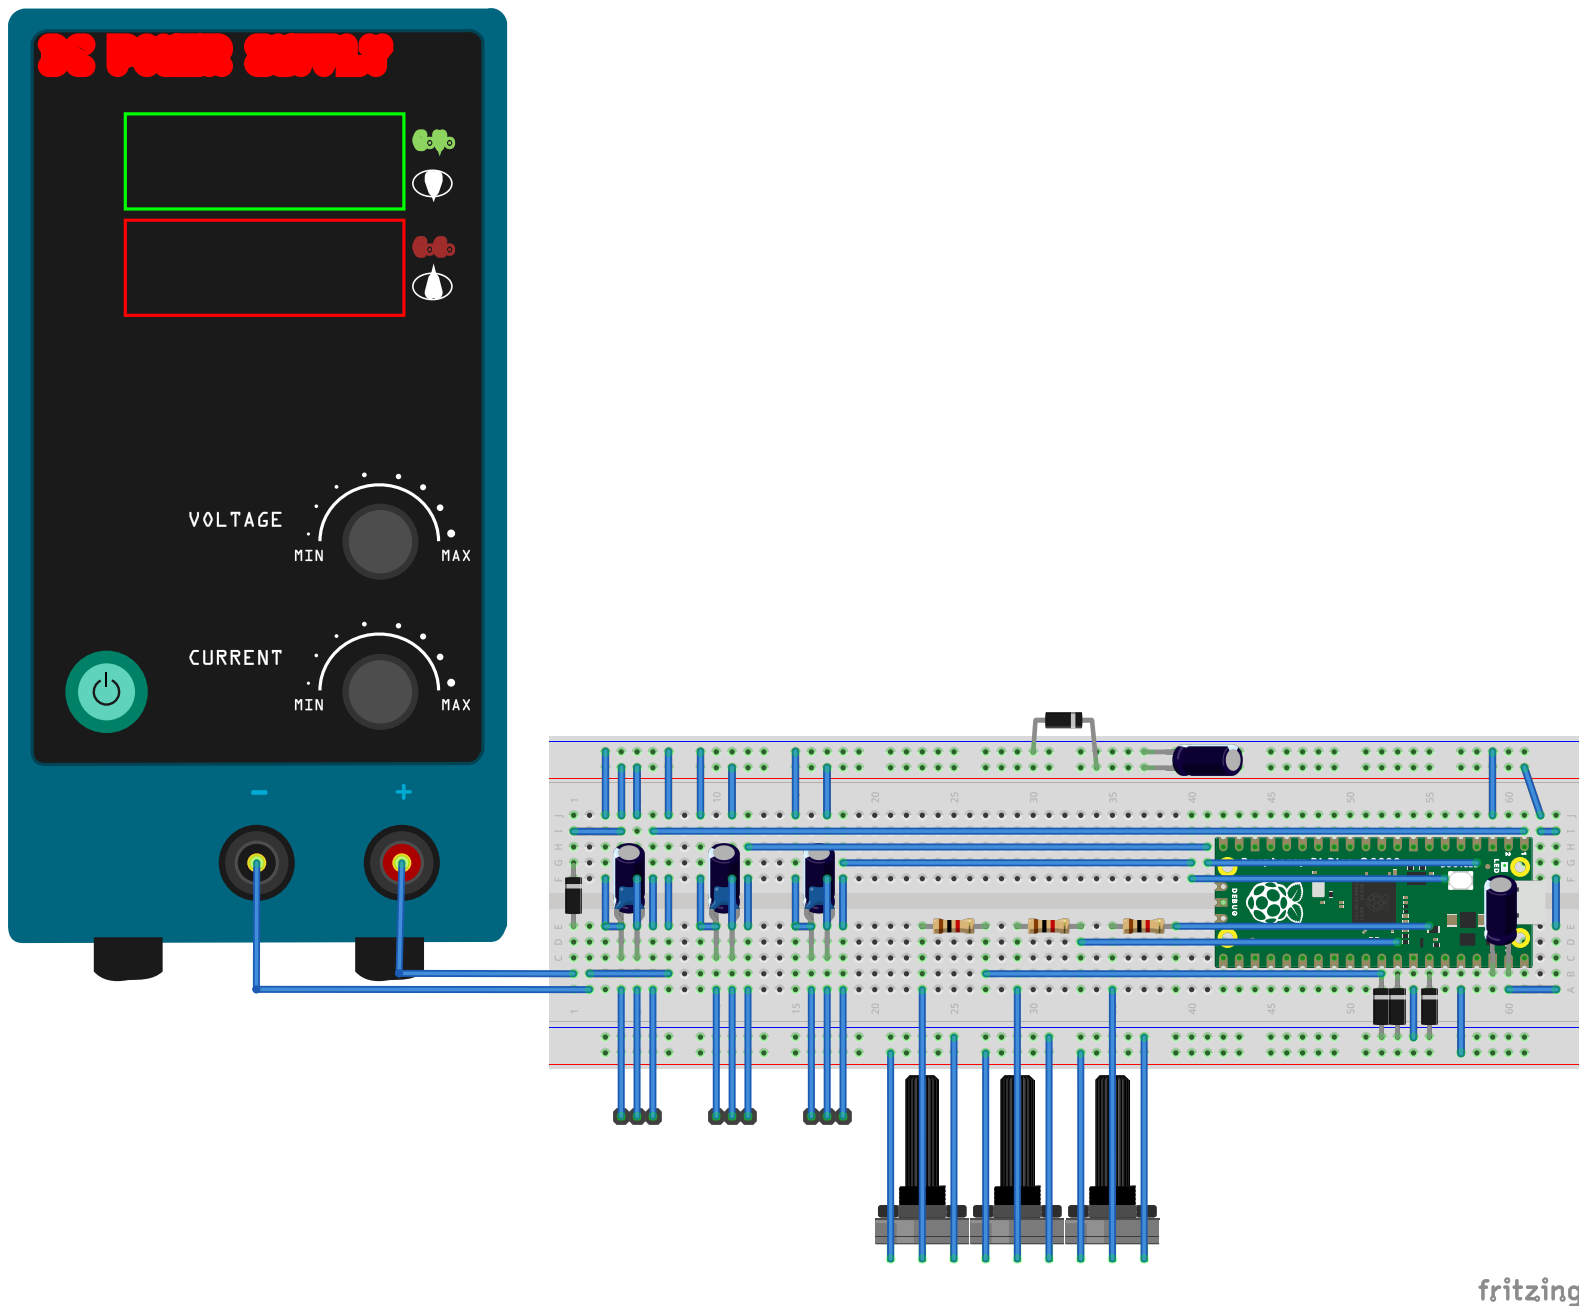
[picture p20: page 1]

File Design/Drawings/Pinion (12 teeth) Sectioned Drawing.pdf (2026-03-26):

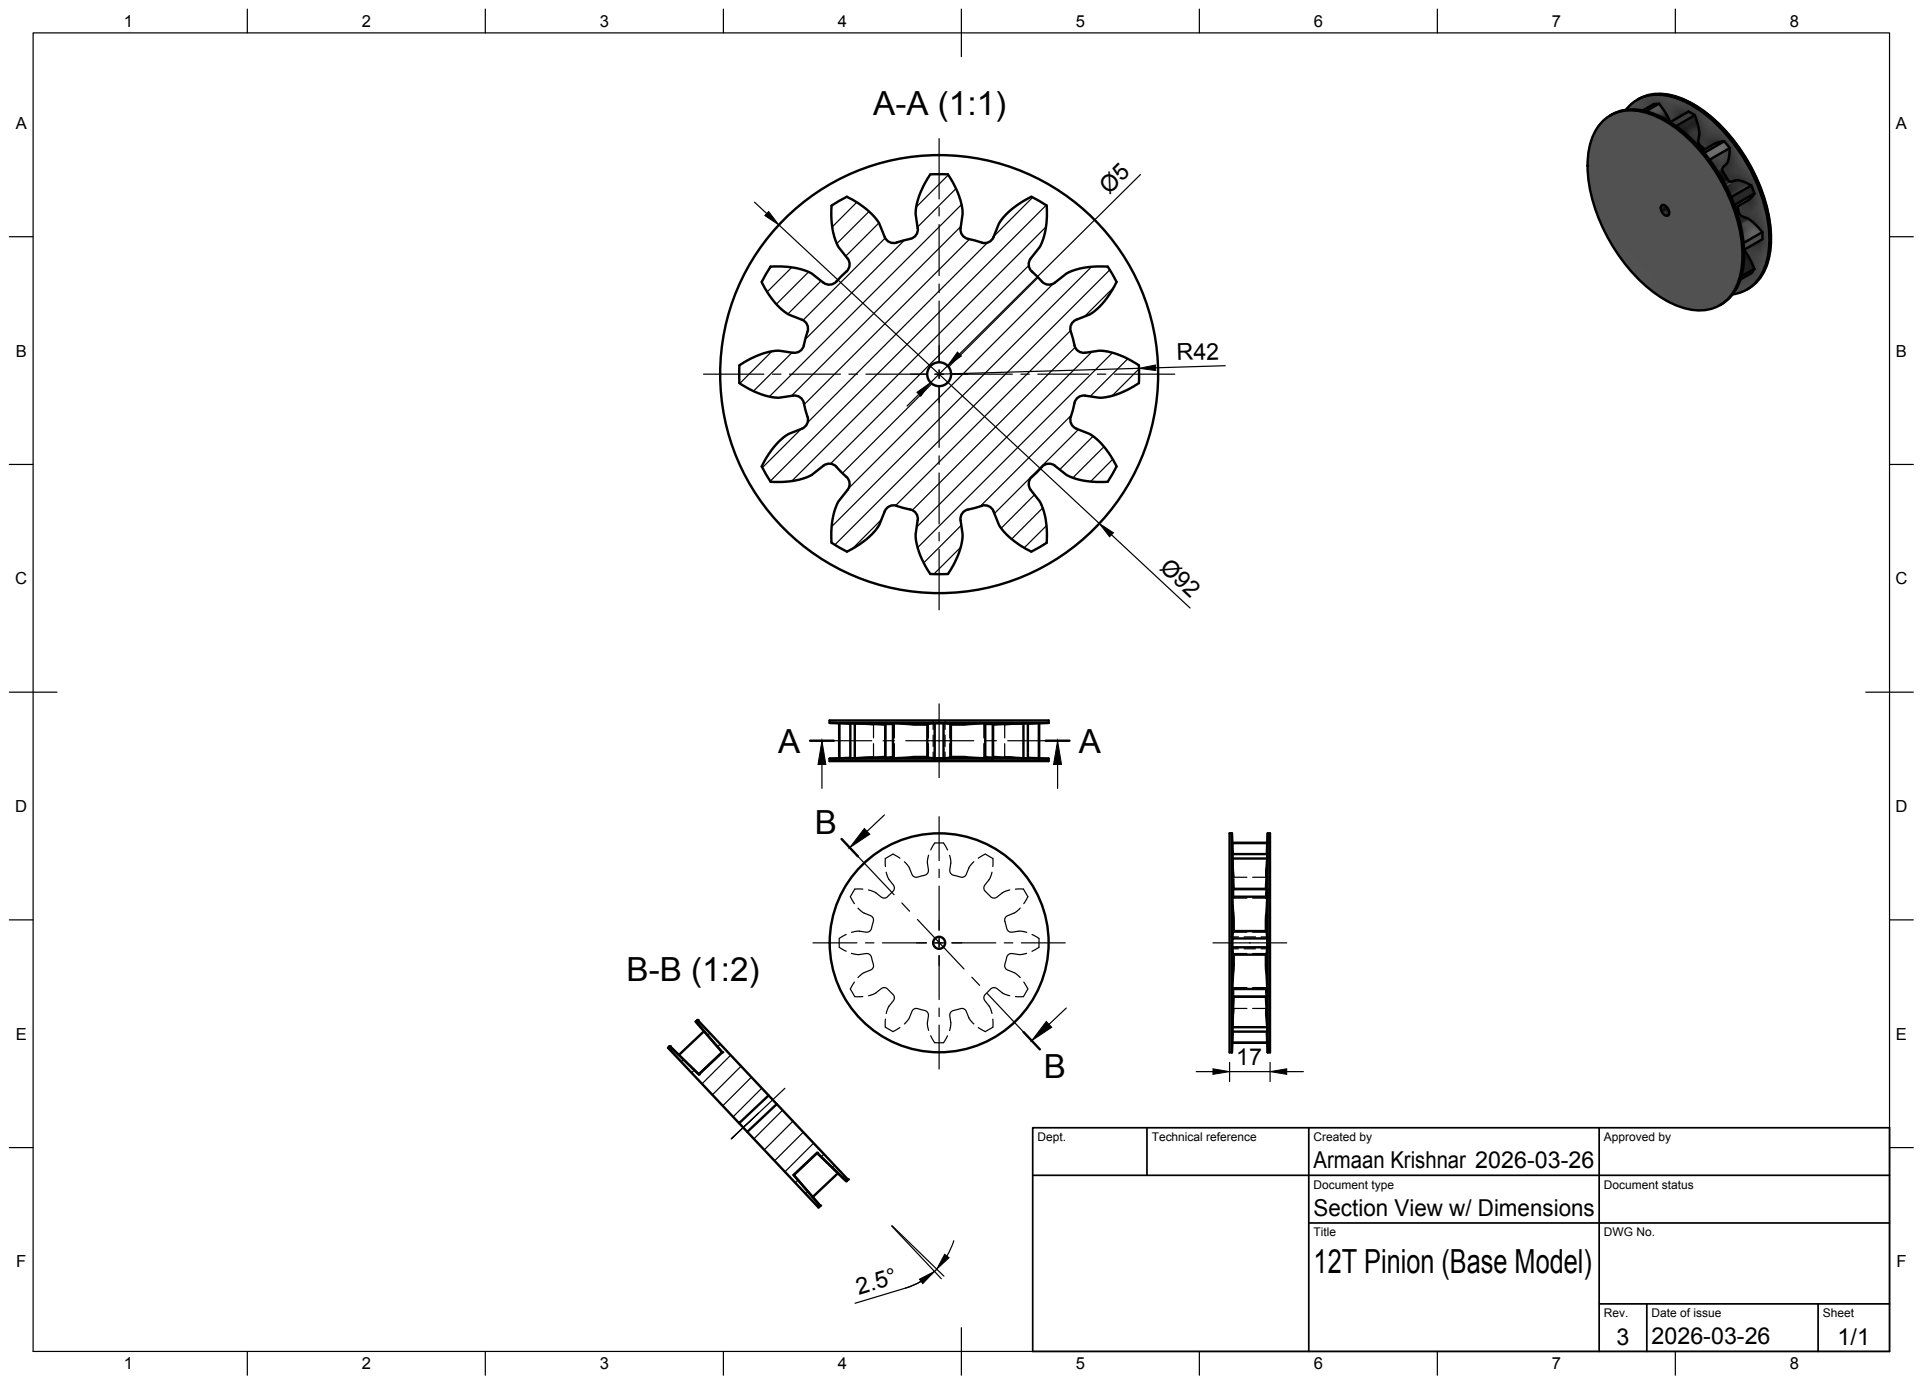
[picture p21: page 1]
Title; DWG No.; Rev.; Date of issue; Sheet

Dept. | Technical reference | Created by Armaan Krishnar 2026-03-26 | Approved by

Document type Section View w/ Dimensions | Document status

12T Pinion (Base Model)

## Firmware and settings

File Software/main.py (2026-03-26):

# EmbRotary - MicroPython controller for Raspberry Pi Pico
#
# Three continuous rotation servos (Feetech FT90R) driven by three
# potentiometers. Each pot controls one servo bidirectionally:
#   - Pot fully CCW  -> full speed one direction   (~1000us pulse)
#   - Pot center     -> stopped                    (~1500us pulse)
#   - Pot fully CW   -> full speed other direction (~2000us pulse)
#
# Wiring:
#   Pot wipers  -> GP26 (ADC0), GP27 (ADC1), GP28 (ADC2)
#   Servo signal-> GP0,         GP2,          GP4
#   Pots        -> 3V3 and GND (in parallel)
#   Servos      -> 5V power rail and GND

from machine import ADC, Pin, PWM
import time

# ---------------------------------------------------------------------------
#                              Configuration
# ---------------------------------------------------------------------------

SERVO_FREQ_HZ   = 50      # Standard servo PWM frequency
PULSE_MIN_US    = 1000    # Full speed, one direction
PULSE_STOP_US   = 1500    # Stopped (neutral)
PULSE_MAX_US    = 2000    # Full speed, other direction

# Width of the center deadband in ADC counts (0-65535).
# Pot values within +/- this amount of center output a stop pulse,
# preventing creep from pot wobble or mechanical center imprecision.
ADC_DEADBAND    = 1200

# ---------------------------------------------------------------------------
#                                Pin setup
# ---------------------------------------------------------------------------

pots = [
    ADC(Pin(26)),   # Pot 1 -> ADC0
    ADC(Pin(27)),   # Pot 2 -> ADC1
    ADC(Pin(28)),   # Pot 3 -> ADC2
]

servos = [
    PWM(Pin(0)),    # Servo 1
    PWM(Pin(2)),    # Servo 2
    PWM(Pin(4)),    # Servo 3
]

for servo in servos:
    servo.freq(SERVO_FREQ_HZ)

# ---------------------------------------------------------------------------
#                             Helper functions
# ---------------------------------------------------------------------------

_PERIOD_US = 1_000_000 // SERVO_FREQ_HZ   # 20000 us at 50 Hz
_ADC_CENTER = 32767

def us_to_duty_u16(pulse_us):
    """Convert a pulse width in microseconds to a 16-bit duty cycle value."""
    return pulse_us * 65535 // _PERIOD_US

def adc_to_pulse_us(adc_val):
    """
    Map a 16-bit ADC reading to a servo pulse width in microseconds.
    A deadband around the center ADC value maps to the stop pulse so
    the servo does not creep when the pot is near center.
    """
    if abs(adc_val - _ADC_CENTER) < ADC_DEADBAND:
        return PULSE_STOP_US
    return PULSE_MIN_US + (adc_val * (PULSE_MAX_US - PULSE_MIN_US)) // 65535

# ---------------------------------------------------------------------------
#                                Main loop
# ---------------------------------------------------------------------------

while True:
    for pot, servo in zip(pots, servos):
        pulse_us = adc_to_pulse_us(pot.read_u16())
        servo.duty_u16(us_to_duty_u16(pulse_us))
    time.sleep_ms(20)   # Update rate matches servo PWM period (50 Hz)

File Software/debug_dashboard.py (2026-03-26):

# EmbRotary - Debug Logger
#
# Compact one-liner debug output for Thonny's shell.
# Columns: raw ADC counts for all three pots, then pulse widths for all three servos.
#
# Run this instead of main.py when diagnosing hardware issues.
# Servos are driven normally throughout — non-intrusive.

from machine import ADC, Pin, PWM
import time

# ---------------------------------------------------------------------------
#                      Configuration (matches main.py)
# ---------------------------------------------------------------------------

SERVO_FREQ_HZ = 50
PULSE_MIN_US  = 1000
PULSE_STOP_US = 1500
PULSE_MAX_US  = 2000
ADC_DEADBAND  = 1200

# ---------------------------------------------------------------------------
#                               Pin setup
# ---------------------------------------------------------------------------

pots   = [ADC(Pin(26)), ADC(Pin(27)), ADC(Pin(28))]
servos = [PWM(Pin(0)),  PWM(Pin(2)),  PWM(Pin(4)) ]

for s in servos:
    s.freq(SERVO_FREQ_HZ)

# ---------------------------------------------------------------------------
#                      Helpers (identical to main.py)
# ---------------------------------------------------------------------------

_PERIOD_US  = 1_000_000 // SERVO_FREQ_HZ
_ADC_CENTER = 32767

def us_to_duty_u16(pulse_us):
    return pulse_us * 65535 // _PERIOD_US

def adc_to_pulse_us(adc_val):
    if abs(adc_val - _ADC_CENTER) < ADC_DEADBAND:
        return PULSE_STOP_US
    return PULSE_MIN_US + (adc_val * (PULSE_MAX_US - PULSE_MIN_US)) // 65535

# ---------------------------------------------------------------------------
#                                Main loop
# ---------------------------------------------------------------------------

print("P1      P2      P3      S1      S2      S3")

while True:
    adc_vals   = []
    pulse_vals = []

    for pot, servo in zip(pots, servos):
        raw      = pot.read_u16()
        pulse_us = adc_to_pulse_us(raw)
        servo.duty_u16(us_to_duty_u16(pulse_us))
        adc_vals.append(raw)
        pulse_vals.append(pulse_us)

    print("{:<8}{:<8}{:<8}{:<8}{:<8}{:<8}".format(*adc_vals, *pulse_vals))
    time.sleep_ms(200)

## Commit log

2026-02-26 Updated `README.md` with current decisions. Added `HardwareSelection.md` with hardware selection justification. Added `\References\` with datasheets relevant to the selected hardware for future refer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
2026-02-28 Added breadboard layout using Fritzing
    [EmbRotary_Circuit.fzz]
2026-03-03 Updated schematic for improved routing in Fritzing
    [EmbRotary_Circuit.fzz]
2026-03-03 Completed V1 of manual schematic routing in Fritzing
    [EmbRotary_Circuit.fzz]
2026-03-03 Added .png of V1 schematic from Fritzing
2026-03-03 First general layout for PCB in Fritzing
    [EmbRotary_Circuit.fzz]
2026-03-13 Added drawing of modelled servo and mount to design directory
2026-03-20 Adjusted `main.py` to clarify calculation order of operations. Added `debug_dashboard.py` to print variables to the console for debugging.
2026-03-20 Added Fusion files for the servo and servo mount measurements.
    [Disc Servo Attachment.f3d, FT90R (Assembly).f3z, Square Servo Attachment.f3d]
2026-03-20 Added hoop, hoop gear, and spur gear Fusion file
    [gear project.f3d]
2026-03-23 Updated mechanics with central spur gear specs
2026-03-23 Added tapered double-flanged 12T pinion and draft assembly documents.
    [Draft Layout Assembly.f3z, Pinion (12 teeth).f3d]
2026-03-26 Added bearing measurements for CAD reference
2026-03-26 Added sectioned drawing for pinion gear dimensions
2026-03-26 Added connector to go between frames
    [20mm Connector Wider.f3z, 20mm Connector.3mf, 20mm Connector_Wider.3mf]
2026-03-26 Added frame for bearings without the servo
    [TestBaseFrictionFit.3mf, TestBaseFrictionFit_Notched.3mf, TestBaseNoServo.3mf]
2026-03-26 Added frame for servo mount. NOTE: Might be an alignment issue with the servo mount, printing to test now
    [TestBaseServo.3mf, TestBaseServo.f3d]
2026-03-26 Reorganized `/Design` directory
    [20mm Connector.3mf, Disc Servo Attachment.f3d, FT90R (Assembly).f3z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]
2026-03-26 Updated Fusion files
    [Draft Layout Assembly.f3z, Pinion (12 teeth).f3d, Pinion (12 teeth).f3z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]
2026-03-26 Cleaned `/Design` directory
    [TestBaseFrictionFit.3mf, TestBaseFrictionFit_Notched.3mf]
2026-03-26 Added bearing-only frame Fusion file
    [TestBaseNoServo.f3d]
2026-03-26 Added BearingPlug to connect axle with inlayed M2 nut
    [BearingPlug.3mf, BearingPlug.f3d, BearingPlugSectioned.3mf]
2026-03-27 Updated servo test base w/ additional cutout for horn mount hardware
    [TestBaseServo.3mf, TestBaseServo.f3d]
2026-03-27 Updated axle design
    [AxleSpacer.3mf, AxleSpacer.f3d, BearingPlug.3mf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]
2026-03-27 Changed base model pinion gear
    [Pinion (12 teeth).3mf]
2026-03-27 Cleaned `/Design` directory. Moved deprecated/abandoned designs to `/Design/Deprecated`.
    [AxleSpacer.3mf, AxleSpacer.f3d, BearingPlug.3mf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]
2026-03-28 Updated BOM
2026-03-29 Added side 1 for the idler pinion, shared with the driver pinion
    [Pinion-Idler-S1.3mf, Pinion-Idler-S1.f3z]
2026-03-29 Added side 2 of the idler pinion
    [Pinion-Idler-S2.3mf, Pinion-Idler-S2.f3z]
2026-03-29 Added print files (.3mf) with settings saved from PrusaSlicer for Prusa i3 MK3S
    [Pinion-Idler-S1.3mf, Pinion-Idler-S2.3mf]
2026-03-29 Added driver pinion which acts as the second side to the matching idler pinion side 1 part
    [Pinion-Driver.3mf, Pinion-Driver.f3z]
2026-03-29 Added single plate printing for both halves of the idler and driver pinion gears.
    [Pinion-Driver.3mf, Pinion-Idler.3mf]
2026-03-29 Created `/Start Building Here` to improve clarity.
    [20mm Connector_Wider.3mf, BaseNoServo.3mf, BaseServo.3mf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]
2026-03-29 Updated with elongated base to avoid interference. Cleaned up directory to improve artist access.
    [20mm Connector Wider.f3z, 20mm Connector_Wider.3mf, 21mm Connector.f3z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]
2026-03-29 Updated assembly diagram and associated `README.md` for building instructions.
